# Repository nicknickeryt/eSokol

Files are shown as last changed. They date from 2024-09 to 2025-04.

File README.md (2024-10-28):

# eSokół
The cheapest possible open source electric bike project built around MY1016Z2 motor and WeAct BlackPill STM32F401CCU6 microcontroller board.\
This is stil WIP. Images and details soon!\
\
[image]\
\
Bike specs:\
Romet "Sokół"\
Year: 1972\
Wheel size: 20" 24H (?)\
Weight (original):\
Weight (current):\
Battery: 7s4p 11.6Ah 29.4V, BMS 25A 10-MOS\
Motor: MY1016Z2 24V 250W (rear-drive)\
Motor driver: LB27 250W\
Motor speed: ~300 RPM max\
Motor torque: ~6.65Nm\
Gears: 16T (rear hub - pedals), 16T (rear-hub - motor), 9T (motor - rear hub)\
Motor - hub gear ratio:  13:16=0,8125\
Output torque: ~8,21\
Vmax: ~20-25 km/h\
Note: the original 9T gear has been replaced with a 13T one.

## Why?
[image]\
Well, I've really wanted to make an electric bicycle for a long time. My goal was to do it cheap and somewhat unique while I'll be learning something new.\
This old Sokół bike was rarely used by me, so it was perfect for this kind of mod, as I also planned to modify an older bike while keeping it as much original-looking as I could.\
\
There were many challenged though. This 20" inch folding bike was really rusty, heavy and wasn't intented to use with this kind of ebike conversion kit. \
This MY1016Z2 kits are probably the cheapest ebike conversion kits out there. They are however intented to be mounted on a special plate on 22"-and-larger-wheeled bicycles. The motor could be mounted easily using its original plate on my bike, but I couldn't pedal. This bike, being a folding one, has a really short chain with a lot of free space from my foot to front wheel, but very little space to the rear end. That's why I had to mount the motor in a such weird way.\
[image]\
\
The battery will be mounted at the rear rack in some kind of metal box, which will also house the microcontroller and PCBs.\
[image]\
\
The original throttle grip handle has been modified, as the motor is too powerful at the moment (9:16 ratio). I've used this great "voltage delay mod" based on an RC filter, you can find it [here](https://electricbike.com/forum/forum/kits/golden-motor-magic-pie/70584-guide-to-hall-sensor-throttle-operation-testing-and-modification). I used slightly different components which gave the best results after playing a lot with different capacitor and resistor values. The acceleration is lower and the motor starts pretty smooth, but it's still quite snappy. It should reduce the motor and its chain stress a great amount. This mod reduced the maximum speed slightly, though (1-1,5km/h), so I've added a switch so I can use the more snappy "sport mode". The switch may eventually be replaced with a MOSFET which gate will be controlled by STM32, but I'm not sure if I really want that extra mode being controlled by the MCU as it adds unnecessary complexity. I've also replaced the handle black rubber and used the bike's original handle. This required some more tuning to the handle, as its outer diameter was a lot larger than the original handle's inner diameter.\
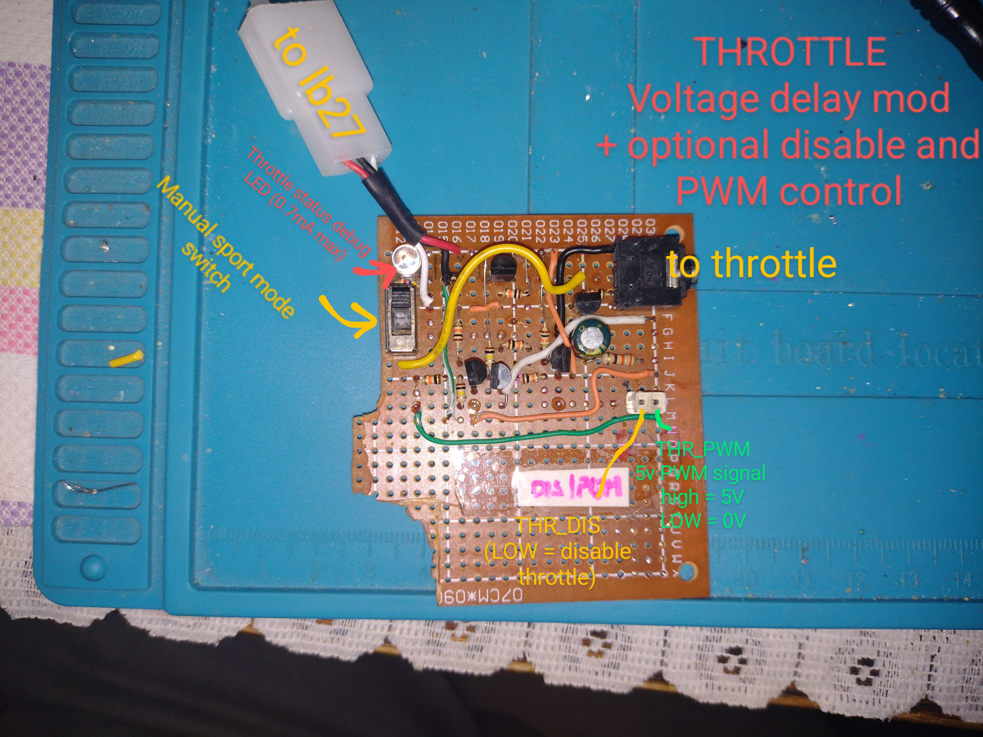
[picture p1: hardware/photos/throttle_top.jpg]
\
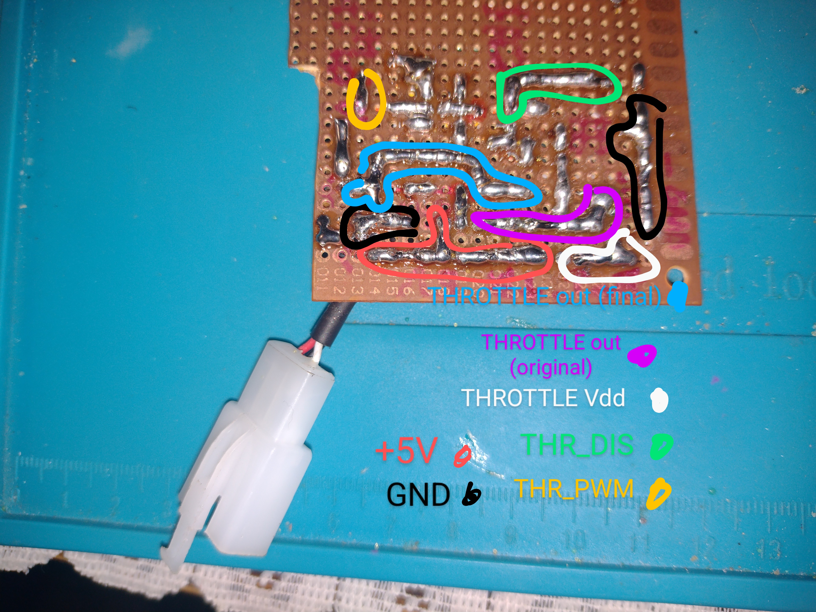
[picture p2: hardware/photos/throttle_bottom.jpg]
\
\
Apart from throttle-based speed control, the bike will also provide the ability to control by pedalling. The microcontroller will read the pedalling speed and provide the LB27 motor controller with enough voltage so that the motor will spin the wheel w little bit faster than the pedals would. This is to make the bike road-legal, which is also a goal of this project.\
\
The lighting system got a little bit of love too. The original front headlight is still used, but modified. Apart from having a single bulb, it now also has four 3.3V LEDs and one bright 18V warm LED. Rear lamp case was broken and would be coverd by the battery housing, so I bought a new one. It will be modified similarily though. There will be 4 leds minimum and a bulb. It will also be possible to power the bulbs via dynamo, but that's a topic for later.\
[image]\
\
The microcontroller, lights, PAS sensor and everything microcontroller-related will be powered by a single 3.6V lithium cell, charged independently from the main battery. This is for safety and simplicity. I want to split the electronics to two parts:\
• big: motor, motor controller, throttle, main battery;\
• LITTLE: display, lighting, PAS sensor, microcontroller, second battery.\
It is also planned for the two systems to be fully independent. Both of them will work with each other, as the microcontroller will at least control the motor speed when using PAS-based speed control, read battery and motors temperatures and voltages and switch between "sport" and smooth mode. However, when the STM32 battery is discharged, it will still be possible to control the motor using the throttle, which is the default control method. If the main battery is flat though, the lighting system will work flawlessly, the display will still provide you with speed, time and distance information.\
\
The bike will be controlled using a screen mounted on the handle. It will provide all the details of a basic speedometer, but will also allow to:\
• toggle lights (with different "animation" styles),\
• switch between PAS-based speed control and a throttle-based one,\
• switch between "sport mode" and smooth mode,\
• read motor and battery voltage and temperature,\
• more?\
\
This repo is currently divided into firmware and hardware parts. In firmware, you will be able to find everything related to the STM32 microcontroller firmware. In hardware, it will be possible to browse different 3d-printable part designs, KiCad schematics and libraries, various images and additional hardware-related files. This repo will be updated soon.

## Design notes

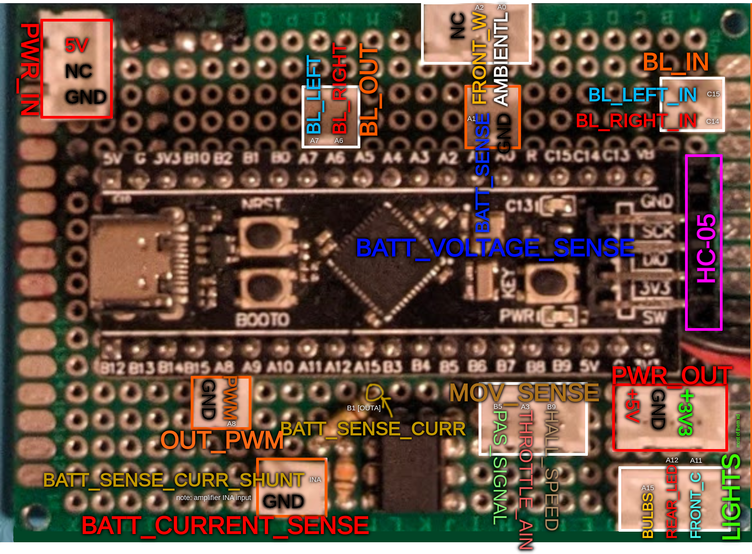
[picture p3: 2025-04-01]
hardware/photos/pinout_sokol.png

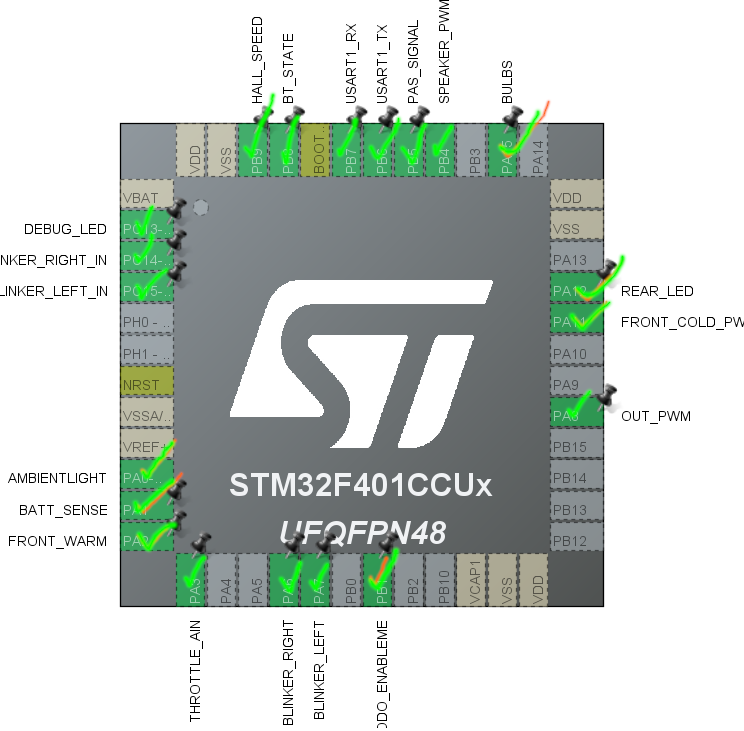
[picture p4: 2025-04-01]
hardware/photos/status_pinout.png

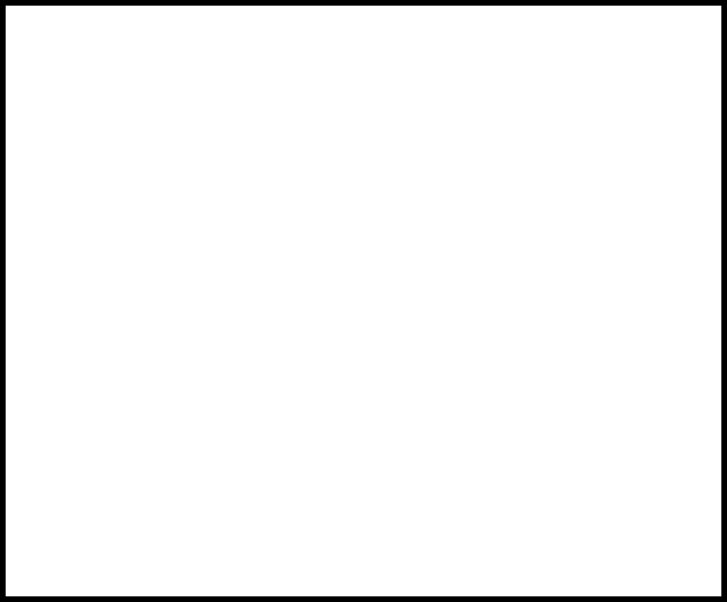
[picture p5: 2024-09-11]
hardware/res/figma/Rectangle 2.png

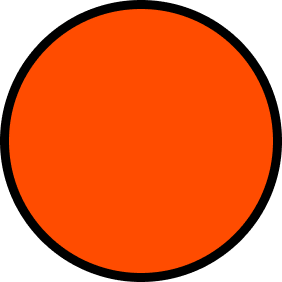
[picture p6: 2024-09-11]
hardware/res/figma/Ellipse 10.png

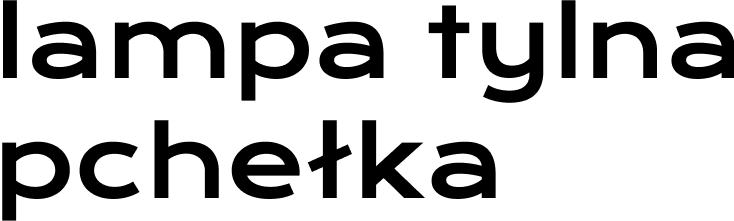
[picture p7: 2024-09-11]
hardware/res/figma/lampa tylna pchełka.png

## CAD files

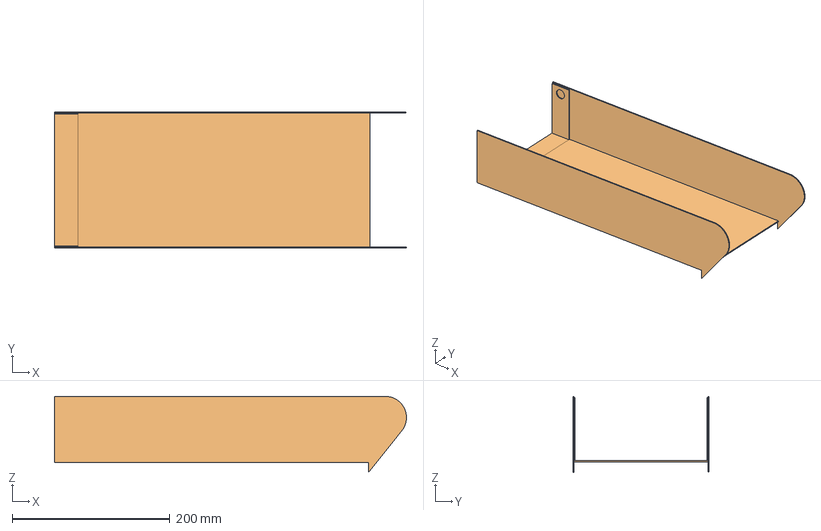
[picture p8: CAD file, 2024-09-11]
hardware/models/rearCase/rearCase.FCStd
446.5 x 173.0 x 96.7 mm
dol
klapa

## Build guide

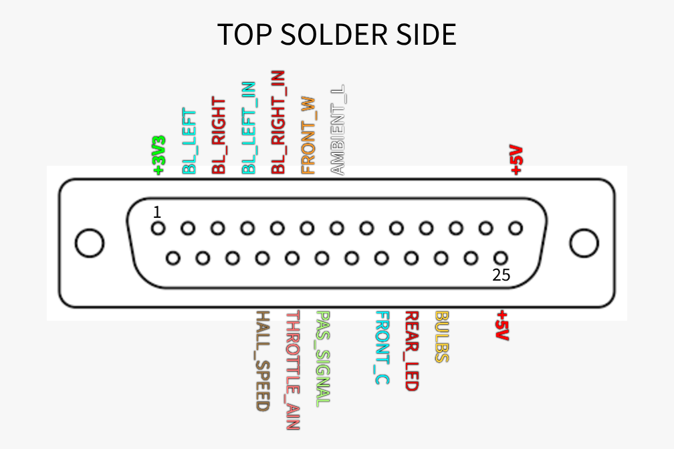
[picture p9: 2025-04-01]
hardware/photos/TOP SOLDER SIDE.png

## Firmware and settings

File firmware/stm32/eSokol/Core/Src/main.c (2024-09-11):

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
/* Includes ------------------------------------------------------------------*/
#include "main.h"

/* USER CODE BEGIN Includes */
#include "ssd1306.h"
#include "ssd1306_fonts.h"
#include "ds3231_for_stm32_hal.h"
#include "stdio.h"
#include "stdbool.h"
/* USER CODE END Includes */

/* USER CODE BEGIN PTD */
const unsigned char logo_romet128_inv[] = { 0x00, 0x00, 0x00, 0x00, 0x00, 0x00,
		0x00, 0x00, 0x00, 0x00, 0x00, 0x00, 0x00, 0x00, 0x00, 0x00, 0x00, 0x00,
		0x00, 0x00, 0x00, 0x00, 0x00, 0x03, 0xFF, 0xFF, 0xFF, 0xFF, 0x00, 0x00,
		0x00, 0x00, 0x00, 0x00, 0x00, 0x00, 0x00, 0x00, 0x00, 0x07, 0xFF, 0xFF,
		0xFF, 0xFE, 0x00, 0x00, 0x00, 0x00, 0x00, 0x00, 0x00, 0x00, 0x00, 0x00,
		0x00, 0x07, 0xFF, 0xFF, 0xFF, 0xFE, 0x00, 0x00, 0x00, 0x00, 0x00, 0x00,
		0x00, 0x00, 0x00, 0x00, 0x00, 0x0F, 0xFF, 0xFF, 0xFF, 0xFC, 0x00, 0x00,
		0x00, 0x00, 0x00, 0x00, 0x00, 0x00, 0x00, 0x00, 0x00, 0x0F, 0xFF, 0xFF,
		0xFF, 0xFC, 0x00, 0x00, 0x00, 0x00, 0x00, 0x00, 0x00, 0x00, 0x00, 0x00,
		0x00, 0x1F, 0xFF, 0xFF, 0xFF, 0xF8, 0x00, 0x00, 0x00, 0x00, 0x00, 0x00,
		0x00, 0x00, 0x00, 0x00, 0x00, 0x1F, 0xFF, 0xFF, 0xFF, 0xF8, 0x00, 0x00,
		0x00, 0x00, 0x00, 0x00, 0x00, 0x00, 0x00, 0x00, 0x00, 0x1F, 0xFF, 0xFF,
		0xFF, 0xF0, 0x00, 0x00, 0x00, 0x00, 0x00, 0x00, 0x00, 0x00, 0x00, 0x00,
		0x00, 0x3F, 0xFF, 0xFF, 0xFF, 0xF0, 0x00, 0x00, 0x00, 0x00, 0x00, 0x00,
		0x00, 0x00, 0x00, 0x00, 0x00, 0x3F, 0xFF, 0xFF, 0xFF, 0xE0, 0x00, 0x00,
		0x00, 0x00, 0x00, 0x00, 0x00, 0x00, 0x00, 0x00, 0x00, 0x7F, 0xFF, 0xFF,
		0x00, 0x3F, 0xFC, 0x00, 0x00, 0x00, 0x00, 0x00, 0x00, 0x00, 0x00, 0x00,
		0x00, 0x7F, 0xFF, 0xFE, 0x00, 0x3F, 0xF8, 0x00, 0x00, 0x00, 0x00, 0x00,
		0x00, 0x00, 0x00, 0x00, 0x00, 0xFF, 0xFF, 0xFE, 0x00, 0x3F, 0xF0, 0x00,
		0x00, 0x00, 0x00, 0x00, 0x00, 0x00, 0x00, 0x00, 0x00, 0xFF, 0xFF, 0xFC,
		0x00, 0x7F, 0xF0, 0x00, 0x00, 0x00, 0x00, 0x00, 0x00, 0x00, 0x00, 0x00,
		0x01, 0xFF, 0xFF, 0xFC, 0x00, 0xFF, 0xE0, 0x00, 0x00, 0x00, 0x00, 0x00,
		0x00, 0x00, 0x00, 0x00, 0x01, 0xFF, 0xFF, 0xFC, 0x00, 0xFF, 0xE0, 0x00,
		0x00, 0x00, 0x00, 0x00, 0x00, 0x00, 0x00, 0x00, 0x01, 0xFF, 0xFF, 0xFF,
		0xFF, 0xFF, 0xC0, 0x00, 0x00, 0x00, 0x00, 0x00, 0x00, 0x00, 0x00, 0x00,
		0x03, 0xFF, 0xFF, 0xFF, 0xFF, 0xFF, 0xC0, 0x00, 0x00, 0x00, 0x00, 0x00,
		0x00, 0x1F, 0xFC, 0x00, 0x03, 0xFF, 0xFF, 0xFF, 0xFF, 0xFF, 0x80, 0x00,
		0x00, 0x00, 0x00, 0x00, 0x00, 0x1F, 0xFF, 0xC0, 0x07, 0xFF, 0xFF, 0xFF,
		0xFF, 0xFF, 0x80, 0x00, 0x00, 0x00, 0x00, 0x00, 0x00, 0x1F, 0xFF, 0xC0,
		0x07, 0xFF, 0xFF, 0xE0, 0x0F, 0xFF, 0x00, 0x00, 0x00, 0x00, 0x00, 0x00,
		0x00, 0x0F, 0xFF, 0xE0, 0x0F, 0xFF, 0xFF, 0xE0, 0x0F, 0xFE, 0x00, 0x00,
		0x00, 0x00, 0x00, 0x00, 0x00, 0x07, 0xFF, 0x00, 0x0F, 0xFF, 0xFF, 0xC0,
		0x0F, 0xFE, 0x00, 0x00, 0x00, 0x00, 0x00, 0x00, 0x00, 0x03, 0xFF, 0x00,
		0x1F, 0xFF, 0xFF, 0xC0, 0x1F, 0xFC, 0x00, 0x00, 0x00, 0x00, 0x00, 0x00,
		0x00, 0x01, 0xFF, 0x00, 0x1F, 0xFF, 0xFF, 0xC0, 0x3F, 0xFC, 0x00, 0x00,
		0x00, 0x00, 0x00, 0x00, 0x00, 0x00, 0xFF, 0x00, 0x1F, 0xFF, 0xFF, 0xFF,
		0xFF, 0xF8, 0x00, 0x00, 0x00, 0x00, 0x00, 0x00, 0x00, 0x02, 0x7F, 0x00,
		0x3F, 0xFF, 0xFF, 0xFF, 0xFF, 0xF0, 0x00, 0x00, 0x00, 0x00, 0x00, 0x00,
		0x00, 0x03, 0xFF, 0x80, 0x3F, 0xFF, 0xFF, 0xFF, 0xFF, 0xF0, 0x00, 0x00,
		0x00, 0x00, 0x00, 0x00, 0x00, 0x03, 0xFF, 0xF0, 0x7F, 0xFF, 0xFF, 0xFF,
		0xFF, 0xE0, 0x00, 0x00, 0x00, 0x00, 0x00, 0x00, 0x00, 0x03, 0xFF, 0xF8,
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

const unsigned char swiatla[] = { 0x00, 0x00, 0x00, 0x00, 0x00, 0x00, 0x01,
		0xF0, 0x39, 0x0C, 0xC2, 0x06, 0x02, 0x03, 0x7A, 0x01, 0x82, 0x01, 0x3A,
		0x03, 0xC2, 0x06, 0x19, 0x1C, 0xE1, 0xF0, 0x00, 0x00, 0x00, 0x00, 0x00,
		0x00 };

const unsigned char muted [] = {
		0x80, 0x00, 0x40, 0x00, 0x01, 0x80, 0x03, 0x0C, 0x02, 0x84, 0x38, 0x86, 0x20, 0x92, 0x00, 0x12,
		0x00, 0x12, 0x20, 0x92, 0x34, 0x86, 0x02, 0x84, 0x03, 0x08, 0x01, 0x80, 0x00, 0x02, 0x00, 0x01
};

/* USER CODE END PTD */

ADC_HandleTypeDef hadc1;

I2C_HandleTypeDef hi2c1;
I2C_HandleTypeDef hi2c2;

TIM_HandleTypeDef htim1;
TIM_HandleTypeDef htim2;
TIM_HandleTypeDef htim3;

void SystemClock_Config(void);
static void MX_GPIO_Init(void);
static void MX_I2C2_Init(void);
static void MX_TIM1_Init(void);
static void MX_TIM2_Init(void);
static void MX_TIM3_Init(void);
static void MX_I2C1_Init(void);
static void MX_ADC1_Init(void);
/* USER CODE BEGIN 0 */

/*
 * -1 nothing
 * 0 main menu
 * 1 settings
 * 2 lightsmenu
 */
int currPage = -1;

int nextPage = -1;

/*
 * -1 nothing
 * 0 toggle headlights
 * 1 toggle sound
 * 2 toggle headlight animation
 *
 */
int nextAction = -1;

/*
 * 0..4 - current menu selection no.
 */
uint8_t nextSel = 0;

uint8_t encPos = 0;
uint8_t encCurPos = 0;

// SETTINGS
bool headlights = false;

volatile uint8_t pulse_count = 0;
uint32_t timeMs = 0;

bool sound = true;

bool anim = true;

int animTimeMs;

int beepTime;

int adcMs;

bool isHeaderEnabled = true;

int timeUpdInt = 1000;

int timeUpdTime;


// batt sense
uint8_t nth_raw = 0;
uint16_t raw[10] = {0};
float voltage = 0;


void stopBeep(){
	 HAL_TIM_PWM_Stop(&htim2, TIM_CHANNEL_2);
}

void beep(int tone) {
	if (!sound)
		return;

	beepTime = HAL_GetTick();
	HAL_TIM_PWM_Start(&htim2, TIM_CHANNEL_2);

	switch (tone) {
	case 0:
		__HAL_TIM_SET_AUTORELOAD(&htim2, 30);
		__HAL_TIM_SET_COMPARE(&htim2, TIM_CHANNEL_2, 15);
		break;
	case 1:
		__HAL_TIM_SET_AUTORELOAD(&htim2, 45);
		__HAL_TIM_SET_COMPARE(&htim2, TIM_CHANNEL_2, 22);
		break;
	case 2:
		__HAL_TIM_SET_AUTORELOAD(&htim2, 50);
		__HAL_TIM_SET_COMPARE(&htim2, TIM_CHANNEL_2, 25);
		break;
	}
}



void formatTime(uint8_t hour, uint8_t minute, char *output) {
    // Sprawdzenie czy godzina jest jednocyfrowa
    if (hour < 10) {
        // Jeśli godzina jest jednocyfrowa, dodaj '0' przed nią
        sprintf(output, "0%d:", hour);
    } else {
        // W przeciwnym razie, zapisz godzinę normalnie
        sprintf(output, "%d:", hour);
    }

    // Sprawdzenie czy minuta jest jednocyfrowa
    if (minute < 10) {
        // Jeśli minuta jest jednocyfrowa, dodaj '0' przed nią
        sprintf(output + 3, "0%d", minute); // +3 bo wtedy zaczynamy od trzeciego znaku
    } else {
        // W przeciwnym razie, zapisz minutę normalnie
        sprintf(output + 3, "%d", minute); // +3 bo wtedy zaczynamy od trzeciego znaku
    }
}

void splitFloat(float num, int *beforeDecimal, int *afterDecimal) {
	*beforeDecimal = (int) num; // Część całkowita
	*afterDecimal = (int) ((num - *beforeDecimal) * 100); // Część ułamkowa
}

void addHeader() {
	if(!isHeaderEnabled) return;


	for (int i=0; i<10; i++) {
		voltage = voltage +  (2 * 3.3 * ((float)raw[i]/4095));
	}
	voltage = voltage/10;


	uint8_t hour = DS3231_GetHour();
	uint8_t minute = DS3231_GetMinute();

	ssd1306_SetCursor(0, 0);
	ssd1306_WriteString("ROMET", Font_6x8, White);

	ssd1306_SetCursor(51, 0);

	char buf[5];
	formatTime(hour, minute, buf);


	ssd1306_WriteString(buf, Font_6x8, White);

	// bottom line
	ssd1306_Line(0, 9, 128, 9, White);

	int beforeDecimal = 0;
	int afterDecimal = 0;
	splitFloat(voltage, &beforeDecimal, &afterDecimal);

	char buf1[2];
	sprintf(buf1,"%d", beforeDecimal);

	char buf2[4];
	sprintf(buf2,"%d", afterDecimal);


	ssd1306_SetCursor(101, 0);
	ssd1306_WriteString(buf1, Font_6x8, White);
	ssd1306_SetCursor(106, 0);
	ssd1306_WriteString(".", Font_6x8, White);
	ssd1306_SetCursor(111, 0);
	ssd1306_WriteString(buf2, Font_6x8, White);

}

void showSettingsPage(int page, int sel, bool blink) {
	beep(1);
	currPage = page;
	int offset = 13;
	ssd1306_Fill(Black);
	addHeader();
	ssd1306_SetCursor(5, offset);

	int y = 21 + offset + sel * 15;
	int y1 = 36 + offset + sel * 15;

	SSD1306_COLOR colors[5] = { 1, 1, 1, 1, 1 };

	if (!blink)
		colors[sel] = 0;

	switch (page) {
	case 1:
		ssd1306_WriteString("Ustawienia", Font_11x18, White);

		ssd1306_Line(0, 21 + offset, 128, 21 + offset, White);

		ssd1306_SetCursor(5, 25 + offset);

		ssd1306_FillRectangle(0, y, 128, y1, !blink);
		ssd1306_WriteString("Swiatla", Font_7x10, colors[0]);
		ssd1306_Line(0, 36 + offset, 128, 36 + offset, White);

		ssd1306_SetCursor(5, 38 + offset);

		ssd1306_WriteString("Hamulce", Font_7x10, colors[1]);
		ssd1306_Line(0, 51 + offset, 128, 51 + offset, White);

		ssd1306_SetCursor(5, 53 + offset);

		ssd1306_WriteString("Dzwiek", Font_7x10, colors[2]);
		ssd1306_Line(0, 66 + offset, 128, 66 + offset, White);

		ssd1306_SetCursor(5, 120);

		ssd1306_WriteString("OK", Font_6x8, White);

		ssd1306_SetCursor(87, 120);
		ssd1306_WriteString("Wstecz", Font_6x8, White);
		break;
	case 2:
		ssd1306_WriteString("Swiatla", Font_11x18, White);

		ssd1306_Line(0, 21 + offset, 128, 21 + offset, White);

		ssd1306_SetCursor(5, 25 + offset);

		ssd1306_FillRectangle(0, y, 128, y1, !blink);
		ssd1306_WriteString("Wlacz/wylacz", Font_7x10, colors[0]);
		ssd1306_Line(0, 36 + offset, 128, 36 + offset, White);

		ssd1306_SetCursor(5, 38 + offset);

		ssd1306_WriteString("Animacje", Font_7x10, colors[1]);
		ssd1306_Line(0, 51 + offset, 128, 51 + offset, White);

		ssd1306_SetCursor(5, 120);

		ssd1306_WriteString("OK", Font_6x8, White);

		ssd1306_SetCursor(87, 120);
		ssd1306_WriteString("Wstecz", Font_6x8, White);
		break;
	}
	ssd1306_UpdateScreen();
}

void addHomeIcons() {
	if (headlights) ssd1306_DrawBitmap(5, 15, swiatla, 16, 16, White);
	if (!sound) 	ssd1306_DrawBitmap(26, 15, muted, 16, 16, White);
}

void showHomescreen(int splash) {
	currPage = 0;
	ssd1306_Init();

	if (splash) {
		ssd1306_Fill(White);
		ssd1306_UpdateScreen();
		ssd1306_Fill(Black);
		ssd1306_UpdateScreen();

		ssd1306_DrawBitmap(0, 0, logo_romet128_inv, 128, 128, White);
		ssd1306_UpdateScreen();

		HAL_Delay(500);
	}

	ssd1306_Fill(Black);

	ssd1306_SetCursor(30, 50);
	ssd1306_WriteString("12.5", Font_16x26, White);

	ssd1306_SetCursor(50, 78);
	ssd1306_WriteString("km/h", Font_7x10, White);

	ssd1306_SetCursor(5, 120);

	ssd1306_WriteString("Menu", Font_6x8, White);

	ssd1306_SetCursor(80, 120);
	ssd1306_WriteString("Swiatla", Font_6x8, White);

	addHeader();

	addHomeIcons();

	ssd1306_UpdateScreen();

	if(!splash) {
		beep(1);
		HAL_Delay(50);
		stopBeep();
		beep(2);
	}
}

void jumpSel(int button) {

	if (currPage == 0)
		nextPage = button == 0 ? 1 : 2;

	else if (currPage == 1) { // settings
		if (button == 1) {
			nextPage = 0;
			return;
		} else if (button == 0) {
			switch(nextSel) {
				case 0:
					nextPage = 2;
					break;
				case 2:
					nextAction = 1;
					break;
			}
		}


	} else if (currPage == 2) { // lights
		if (button == 1) {
			nextPage = 0;
			return;
		} else if (button == 0) {

			switch(nextSel) {
				case 0:
					nextAction = 0;
					break;
				case 1:
					nextAction = 2;
					break;
			}
		}
	}

}

void HAL_GPIO_EXTI_Callback(uint16_t GPIO_Pin) {
	if (GPIO_Pin == GPIO_PIN_1 && ((HAL_GetTick() - timeMs) > 150)
			&& HAL_GPIO_ReadPin(GPIOB, GPIO_Pin) == 0) // If The INT Source Is EXTI Line9 (A9 Pin)
					{
		jumpSel(0);
		timeMs = HAL_GetTick();
	} else if (GPIO_Pin == GPIO_PIN_0 && ((HAL_GetTick() - timeMs) > 150)
			&& HAL_GPIO_ReadPin(GPIOB, GPIO_Pin) == 0) // If The INT Source Is EXTI Line9 (A9 Pin)
					{
		jumpSel(1);
		timeMs = HAL_GetTick();
	}
}

/* USER CODE END 0 */

/**
  * @brief  The application entry point.
  * @retval int
  */
int main(void)
{

  /* MCU Configuration--------------------------------------------------------*/

  /* Reset of all peripherals, Initializes the Flash interface and the Systick. */
  HAL_Init();

  /* Configure the system clock */
  SystemClock_Config();

  /* Initialize all configured peripherals */
  MX_GPIO_Init();
  MX_I2C2_Init();
  MX_TIM1_Init();
  MX_TIM2_Init();
  MX_TIM3_Init();
  MX_I2C1_Init();
  MX_ADC1_Init();
  /* USER CODE BEGIN 2 */


  	DS3231_Init(&hi2c1);

	HAL_TIM_Encoder_Start(&htim1, TIM_CHANNEL_ALL);

	beep(0);

	showHomescreen(1);

	ssd1306_SetContrast(255);

	beep(1);
	HAL_Delay(25);
	stopBeep();
	HAL_Delay(25);
	beep(1);

	animTimeMs = timeUpdTime = HAL_GetTick();
	adcMs = -5001;


	/*
	 showSettings();

	 HAL_Delay(1500);*/

	bool bylo = 0;
  /* USER CODE END 2 */

  /* Infinite loop */
  /* USER CODE BEGIN WHILE */
	while (1) {
		// periodical voltage check
		if (HAL_GetTick() - adcMs > 800 && !bylo) {
			HAL_GPIO_WritePin(GPIOA, GPIO_PIN_11, GPIO_PIN_SET);
			bylo = 1;
		}
		if( HAL_GetTick() - adcMs > 1000) {
			nth_raw=nth_raw == 10 ? 0 : nth_raw + 1;
			HAL_ADC_Start(&hadc1);
			if(HAL_ADC_PollForConversion(&hadc1, 10) == HAL_OK) {
				raw[nth_raw] = HAL_ADC_GetValue(&hadc1);
			}
			HAL_ADC_Stop(&hadc1);
			adcMs=HAL_GetTick();
			//HAL_GPIO_WritePin(GPIOA, GPIO_PIN_11, GPIO_PIN_RESET);
			bylo=0;
		}



		if(HAL_GetTick() - beepTime > 50 ) stopBeep();

		if(HAL_GetTick() - timeUpdTime > timeUpdInt ) {
			addHeader();
			ssd1306_UpdateScreen();
		}


		encCurPos = TIM1->CNT;
		if ((encCurPos != encPos) && (currPage != 0)) {
			nextSel = encCurPos % 5;
			showSettingsPage(currPage, nextSel, 0);
			encPos = encCurPos;
		}

		if (nextPage != -1) {
			switch (nextPage) {
			case 0:
				showHomescreen(0);
				TIM1->CNT = nextSel = encCurPos = encPos = 0;
				break;
			case 1:
				showSettingsPage(nextPage, nextSel, 0);
				break;
			case 2:
				showSettingsPage(nextPage, nextSel, 0);
				break;
			}
			nextPage = -1;
		}

		if (nextAction != -1) {
			switch (nextAction) {
			case 0:
				if (headlights) {
					headlights = false;
					HAL_TIM_PWM_Stop(&htim3, TIM_CHANNEL_1);
				} else {
					headlights = true;
					HAL_TIM_PWM_Start(&htim3, TIM_CHANNEL_1);
					htim3.Instance->CCR1 = 255;
				}
				showSettingsPage(currPage, nextSel, 1);
				showSettingsPage(currPage, nextSel, 0);
				break;

			case 1:
				showSettingsPage(currPage, nextSel, 1);
				showSettingsPage(currPage, nextSel, 0);
				sound = sound == true ? false: true;
				break;
			case 2:
				showSettingsPage(currPage, nextSel, 1);
				showSettingsPage(currPage, nextSel, 0);
				anim = anim == true ? false: true;
				htim3.Instance->CCR1 = 255;
				break;
			}
			nextAction = -1;
		}

		// todo zmienic na switch zeby bylo szybciej
		if(headlights && anim) {
			if(HAL_GetTick() - animTimeMs > 1200) {
				htim3.Instance->CCR1 = 255;
				animTimeMs = HAL_GetTick();
			}
			else if(HAL_GetTick() - animTimeMs > 1100) {
				htim3.Instance->CCR1 = 220;
			}
			else if(HAL_GetTick() - animTimeMs > 1000) {
				htim3.Instance->CCR1 = 200;
			}
			else if(HAL_GetTick() - animTimeMs > 900) {
				htim3.Instance->CCR1 = 180;
			}
			else if(HAL_GetTick() - animTimeMs > 800) {
				htim3.Instance->CCR1 = 160;
			}
			else if(HAL_GetTick() - animTimeMs > 700) {
				htim3.Instance->CCR1 = 140;
			}
			else if(HAL_GetTick() - animTimeMs > 600) {
				htim3.Instance->CCR1 = 120;
			}
			else if(HAL_GetTick() - animTimeMs > 500) {
				htim3.Instance->CCR1 = 100;
			}
			else if(HAL_GetTick() - animTimeMs > 400) {
				htim3.Instance->CCR1 = 80;
			}
			else if(HAL_GetTick() - animTimeMs > 300) {
				htim3.Instance->CCR1 = 60;
			}
			else if(HAL_GetTick() - animTimeMs > 200) {
				htim3.Instance->CCR1 = 40;
			}
			else if(HAL_GetTick() - animTimeMs > 100) {
				htim3.Instance->CCR1 = 20;
			}
			else {
				htim3.Instance->CCR1 = 0;
			}

		}


    /* USER CODE END WHILE */

    /* USER CODE BEGIN 3 */
	}
  /* USER CODE END 3 */
}

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


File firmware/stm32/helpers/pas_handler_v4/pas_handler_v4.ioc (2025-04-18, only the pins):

Mcu.UserName=STM32F401CCUx
PA0-WKUP.GPIO_Label=AMBIENTLIGHT
PA0-WKUP.Signal=ADCx_IN0
PA1.GPIO_Label=BATT_SENSE
PA1.Signal=ADCx_IN1
PA11.GPIO_Label=FRONT_COLD_PWM
PA11.Signal=S_TIM1_CH4
PA12.GPIO_Label=REAR_LED
PA12.Signal=GPIO_Output
PA15.GPIO_Label=BULBS
PA15.Signal=GPIO_Output
PA2.GPIO_Label=FRONT_WARM
PA2.Signal=GPIO_Output
PA3.GPIO_Label=THROTTLE_AIN
PA3.Signal=ADCx_IN3
PA4.GPIO_Label=SPI1_CS
PA4.Signal=GPIO_Output
PA5.Signal=SPI1_SCK
PA6.Signal=SPI1_MISO
PA7.Signal=SPI1_MOSI
PA8.GPIO_Label=OUT_PWM
PA8.Signal=S_TIM1_CH1
PB0.GPIO_Label=BLINKER_RIGHT
PB0.Signal=GPIO_Output
PB1.GPIO_Label=BATT_CURR_TODO_ENABLEME
PB1.Signal=ADCx_IN9
PB10.GPIO_Label=BLINKER_LEFT
PB10.Signal=GPIO_Output
PB4.GPIO_Label=SPEAKER_PWM
PB4.Signal=S_TIM3_CH1
PB5.GPIO_Label=PAS_SIGNAL
PB5.Signal=GPXTI5
PB6.Signal=USART1_TX
PB7.Signal=USART1_RX
PB8.GPIO_Label=BT_STATE
PB8.Signal=GPXTI8
PB9.GPIO_Label=HALL_SPEED
PB9.Signal=GPXTI9
PC13-ANTI_TAMP.GPIO_Label=DEBUG_LED
PC13-ANTI_TAMP.Signal=GPIO_Output
PC14-OSC32_IN.GPIO_Label=BLINKER_RIGHT_IN
PC14-OSC32_IN.Signal=GPXTI14
PC15-OSC32_OUT.GPIO_Label=BLINKER_LEFT_IN
PC15-OSC32_OUT.Signal=GPXTI15

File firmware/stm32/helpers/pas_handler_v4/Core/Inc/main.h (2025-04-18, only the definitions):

#define DEBUG_LED_Pin GPIO_PIN_13
#define DEBUG_LED_GPIO_Port GPIOC
#define BLINKER_RIGHT_IN_Pin GPIO_PIN_14
#define BLINKER_RIGHT_IN_GPIO_Port GPIOC
#define BLINKER_RIGHT_IN_EXTI_IRQn EXTI15_10_IRQn
#define BLINKER_LEFT_IN_Pin GPIO_PIN_15
#define BLINKER_LEFT_IN_GPIO_Port GPIOC
#define BLINKER_LEFT_IN_EXTI_IRQn EXTI15_10_IRQn
#define AMBIENTLIGHT_Pin GPIO_PIN_0
#define AMBIENTLIGHT_GPIO_Port GPIOA
#define BATT_SENSE_Pin GPIO_PIN_1
#define BATT_SENSE_GPIO_Port GPIOA
#define FRONT_WARM_Pin GPIO_PIN_2
#define FRONT_WARM_GPIO_Port GPIOA
#define THROTTLE_AIN_Pin GPIO_PIN_3
#define THROTTLE_AIN_GPIO_Port GPIOA
#define SPI1_CS_Pin GPIO_PIN_4
#define SPI1_CS_GPIO_Port GPIOA
#define BLINKER_RIGHT_Pin GPIO_PIN_0
#define BLINKER_RIGHT_GPIO_Port GPIOB
#define BATT_CURR_TODO_ENABLEME_Pin GPIO_PIN_1
#define BATT_CURR_TODO_ENABLEME_GPIO_Port GPIOB
#define BLINKER_LEFT_Pin GPIO_PIN_10
#define BLINKER_LEFT_GPIO_Port GPIOB
#define OUT_PWM_Pin GPIO_PIN_8
#define OUT_PWM_GPIO_Port GPIOA
#define FRONT_COLD_PWM_Pin GPIO_PIN_11
#define FRONT_COLD_PWM_GPIO_Port GPIOA
#define REAR_LED_Pin GPIO_PIN_12
#define REAR_LED_GPIO_Port GPIOA
#define BULBS_Pin GPIO_PIN_15
#define BULBS_GPIO_Port GPIOA
#define SPEAKER_PWM_Pin GPIO_PIN_4
#define SPEAKER_PWM_GPIO_Port GPIOB
#define PAS_SIGNAL_Pin GPIO_PIN_5
#define PAS_SIGNAL_GPIO_Port GPIOB
#define PAS_SIGNAL_EXTI_IRQn EXTI9_5_IRQn
#define BT_STATE_Pin GPIO_PIN_8
#define BT_STATE_GPIO_Port GPIOB
#define BT_STATE_EXTI_IRQn EXTI9_5_IRQn
#define HALL_SPEED_Pin GPIO_PIN_9
#define HALL_SPEED_GPIO_Port GPIOB
#define HALL_SPEED_EXTI_IRQn EXTI9_5_IRQn

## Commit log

2024-09-11 Upload old FreeCad rear case design
    [rearCase.FCStd]
2024-09-12 hardware: schematics: Fix improper NMOS placement, misc minor fixes
    [eSokol.kicad_sch, hall.kicad_sch, mcu.kicad_sch]
2024-09-13 Fix throttle transistor layout once more, move throttle to a separate page. Still needs testing.
    [eSokol.kicad_sch, mcu.kicad_sch, throttle.kicad_sch]
2024-09-23 schematics: (almost) finalize throttle circuit (it's working :D), minor cleanups
    [eSokol.kicad_sch, mcu.kicad_sch, throttle.kicad_sch]
2024-09-23 Update README.md
    Add credits for voltage delay mod
2024-09-23 Upload throttle mod circuit photos
2024-09-23 Add throttle mod photos to readme, minor improvements, clarify on the sport mode switch
2024-09-30 Update throttle circuits, move bigbatt to its own sheet and design ds-vc288 circuit
    [bigbatt.kicad_sch, eSokol.kicad_sch, throttle.kicad_sch]
2024-09-30 Add measurements from 29.09.2024, add some todos in throttle schematics
    [throttle.kicad_sch]
2024-09-30 Move main stm32 firmware to its own eSokol directory, upload pas_handler_v2_pwm helper code
2024-10-05 Create one BIG schematic containing everything related to motor and its driver
    [big.kicad_sch, eSokol.kicad_sch, fan.kicad_sch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]
2024-10-08 Initial TCRT5000-based rider detect, rearrange MCU pin layout
    [mcu.kicad_sch]
2024-10-08 Upload stm32f401ccu6 ioc based on current mcu schematic
2024-10-12 Minor lights fixes and improvements, added decoupling cap to mcu 5V, removed unused files
    [RTC.kicad_sch, bell.kicad_sch, bigbatt.kicad_sch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]
2024-10-12 Update pas_handler_v2_pwm firmware helper: add switch disabling and enabling algorithm and throttle, add 3.3 to algorithm equation, make the algorithm wait for 5 wheel turns, minor fixes and cleaups
    [main.c, main.h, pas_handler_v2_pwm.ioc]
2024-10-12 Update on the new motor sprocket and maximum speed
2024-10-12 Upload ds18b20_mot temperature-based motor cooling fan controller firmware helpere
2024-10-19 Upload the new pas_handler_v3 cmake-based project with basic uart communication
2024-10-23 schematics: eSokol: big: replace SW_SPORT with digital THR_SPORT input
    [big.kicad_sch, mcu.kicad_sch]
2024-10-27 Add sounds & custom gpio HAL, refactor the whole project, better uart communication, beautify code, convert everything to non-blocking,
2024-10-30 pas_handler_v3: move init stuff to bikeInit, send random velocity data for testing
2024-10-30 pas_handler_v3: added frontColdLED brightness control, fixed sound stuff, add bulbs toggle, clarify about status command
    [animations.c, commands.c, gpio.c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]
2024-11-09 Add matlab helper for buzzer RC filter Bode plots
2024-11-09 hardware/schematics: Replace screen-based control for HC-05 smartphone-app-based control, add buzzer RC filter, rework cold LED circuit
    [buzzer.kicad_sch, eSokol.kicad_sch, lights.kicad_sch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]
2024-11-09 Remove leftover OLED buttons
    [mcu.kicad_sch]
2024-11-09 pas_handler_v3: increase initial LED brightness, enable sound by default (again)
2024-11-09 pas_handler_v3: use defined timer macros, minor improvements
2024-11-09 pas_handler_v3: switch to 2-1 prescaler for TIM1 & adapt algorithm values,
2024-11-09 pas_handler_v3: add periodical 1s status send Hopefully this won't affect algorithm's time...
    [uart.c]
2024-11-09 pas_handler_v3: fix memory leak malloc was called in every call of sendStatus() without freeing causing a memory leak
    [commands.c, helpers.c]
2024-11-09 pas_handler_v3: change shouldSendStatus1sTime type from uint16_t to uint32_t to prevent overflowing
    [uart.c]
2024-11-10 pas_handler_v3: fix another malloc memory leak
    [helpers.c]
2024-11-22 pas_handler_v3: initial speed sensor stuff
2024-11-24 pas_handler_v3: polishing up * Improved logDebugXXX handling * Finished hall speed sensor stuff * Added new helper function: float_to_char(float) * Renamed multiple variable/function names for readab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
2024-11-24 Added algorithm equation component control command, added error sound, minor fixes around debug mode
    [algorithm.c, algorithm.h, commands.c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]
2024-11-25 hardware/schematics: update mcu and big schematics to reflect current project state
    [big.kicad_sch, mcu.kicad_sch]
2024-11-25 pas_handler_v3: added adc battery voltage handler: measure, format and send in status
2024-12-04 hardware/schematics: add initial blinkers and brake handler circuits
    [lights.kicad_sch, mcu.kicad_sch]
2024-12-04 hardware/schematics: finish-ify blinkers circuit, mark old blinkers circuit as outdated
    [blinkers.kicad_sch, lights.kicad_sch]
2024-12-08 pas_handler_v3: blinkers finished, ambient light, proper DMA ADC handling, more fixes and improvements * ADC is now properly handled using DMA in its own file and it is using proper continuous scan m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
    [adc.c, adc.h, algorithm.c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]
2024-12-09 hardware/schematics: updated eSokol to reflect new features: ambient light LDR sensor and blinkers Remove old NE555-based blinkers circuit too
    [blinkers.kicad_sch, eSokol.kicad_sch, lights.kicad_sch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]
2025-04-01 LB27 PWM remake
    [LB27_PWM.kicad_pcb, LB27_PWM.kicad_sch]
2025-04-01 WIP: update some schematics to reflect the newest design changes
    [big.kicad_sch, buzzer.kicad_sch, dynamo.kicad_sch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]
2025-04-02 Send status every 100ms Hopefully this doesn't affect MCU performance that much
    [uart.c]
2025-04-02 Increase adc sampling time/avg amount to smoothen measurements, disable pull-ups on blinker output pins
2025-04-15 Decrease adc sampling time (well...)
2025-04-15 New throttle algorithm, remove PAS algorithm temporarily, minor code cleanups
2025-04-15 Add new throttle algorithm matlab simulation
2025-04-17 Move velocity measurement to speedometer.h, minor cleanups
2025-04-17 General refactor part 3: adc improvements
2025-04-19 Odometer: fix writing bug * we should first increase flash slot and only then write to empty slot * if we erase the whole sector, we should write to first flash slot so we don't lose current distance
    [odometer.c]
2025-04-19 helpers: add ema filter and clamp helpers

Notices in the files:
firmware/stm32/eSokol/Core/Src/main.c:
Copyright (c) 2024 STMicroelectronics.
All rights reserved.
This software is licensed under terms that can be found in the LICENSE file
